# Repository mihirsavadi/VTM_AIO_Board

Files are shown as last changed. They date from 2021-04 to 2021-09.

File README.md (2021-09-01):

# All-in-One Board | Virginia Tech Motorsports



This repository contains all documentation and material related to [Virginia Tech's Formula SAE team - Virginia Tech Motorsports](https://vtmotorsports.weebly.com/) - All-in-One board for our 2021/2022 internal combustion vehicle.

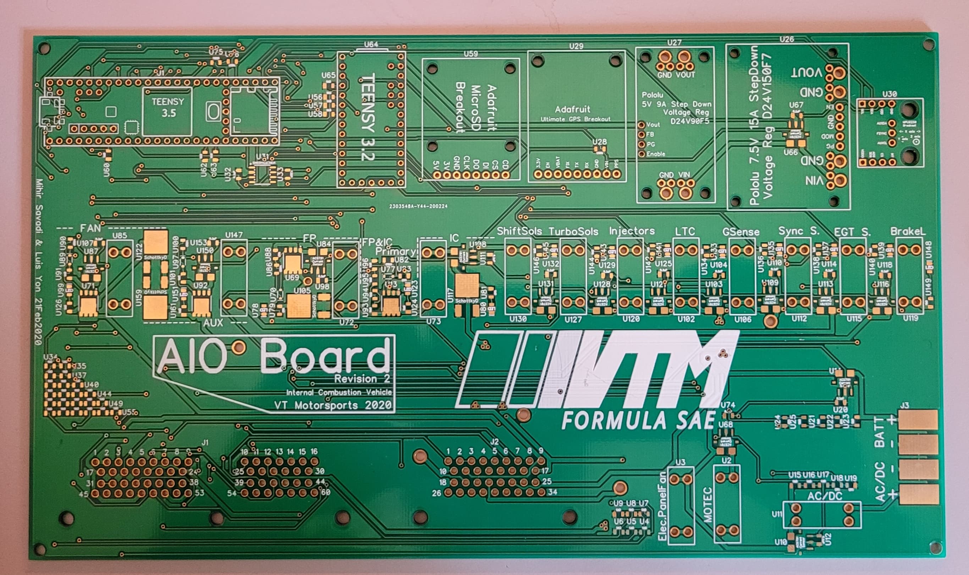
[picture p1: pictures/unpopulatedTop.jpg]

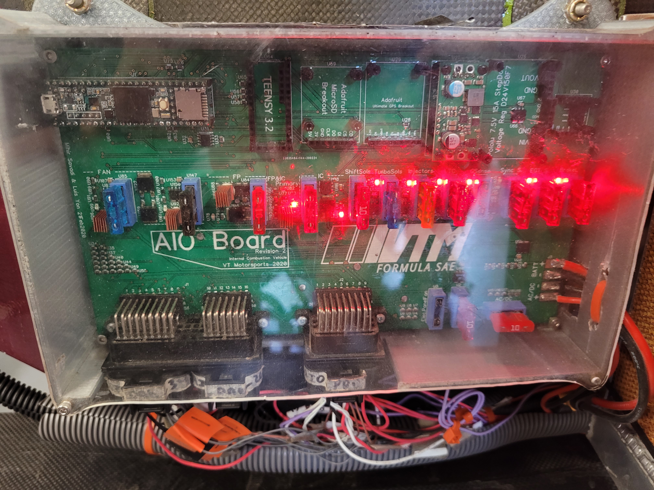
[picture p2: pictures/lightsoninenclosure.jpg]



The AIO board encapsulates several data acquisition features, as well as rules compliant power staging and power distribution, into a single PCB. Note that it is tightly integrated with our Brake-System-Plausibility device which can be found at the repository over [here](https://vtmotorsports.weebly.com/). 

The repository is split into [hardware](./hardware) and [software](./software) subdirectories. The former contains schematics, BOM, etc. Note that I used Diptrace as my PCB design software of choice, and while all critical files for board fabrication/inventory management are available in standard formats (GERBER, pdf's, spreadsheets), the original Diptrace files are included as well. The rest of the team uses Altium, however I prefer Diptrace - its easy to port between the two. The software directory contains Platform-IO project files that run both the MAIN and DRS microcontrollers on the AIO board. Custom Hardware Abstraction Layers/API's were made in order to make it easy to work with the board's slew of features. Both subdirectories include folders containing all our old revisions, which can be safely ignored unless you are a VTM member and/or are curious about the evolution of our design process.  

Running our microcontrollers with the Arduino bootloader and its general hardware abstraction layer not only allows us access to a vast array of arduino compatible easy-to-use libraries for various embedded hardware components (saving us dev time), but also allows lesser experienced team members to absorb functionality and hit the ground running with contribution quicker. We suffer from little to nothing when it comes to the typical drawbacks of using the arduino abstraction layer because 1. we are using proven and optimized hardware by standardizing to the teensy line of microcontrollers, 2. we are not using the stock arduino IDE, rather platform IO which is an extremely rich and ever-expanding IDE for a vast array of embedded processors and development boards, allowing us to easily and reliably integrate custom as well as off-the-shelf open source libraries, and 3. all of our applications are low speed and low memory.  

## Software Guide

Please read all the code in the /src directories for both the AIO_MAIN_MCU and AIO_DRS_MCU to understand the system thoroughly and before attempting to modify any code. All pin/IO definitions for the microcontrollers are established as macros in a file called "pin_definitions.hpp" in both directories, please study these and compare them with the schematics in the hardware subdirectories. Only use these macros for pin control in the code in order to keep things consistent, clean, and less error prone. Also remember to see header comments in order to match code and hardware compatibility - everything in the top level directories by default should be compatible with the latest hardware revision, which as of writing this is 'DAQ_PDU AIO BOARD REV2'.

In order to get an idea of how to use the various libraries to interact with peripherals on the AIO (SD card, GPS, IMU), read the documentation and example arduino sketches in the lib_dep directory. So for the MAIN MCU this would be [.pio\libdeps\teensy35](./software/AIO_MAIN_MCU/.pio/libdeps/teensy35)

If you want to add libraries, please visit the Platform-IO libraries registry and add the dependency into our project's 'platformio.ini' file. [This video](https://www.youtube.com/watch?v=buFKeqbafDI) illustrates this nicely. This file basically configures every option about our project - the serial port baud rate, library dependencies, what board etc were using, everything. Its a very powerful tool.  

Note that the arduino hardware abstraction layer compiles C++, but in reality most things are in C. The only significant usable C++ features are classes. Absolutely nothing from the C++ standard library should be used as it will wreck your boards memory and probably cause stack fragmentation which will either brick or freeze your board, which will be hard to debug. You can get away with using an std::string or an std::vector here or there but since its such a nasty slippery slope that hits quick stay away from it at all costs. So if you want to use convenient C++ like data structures (besides classes or structs) I recommend you don't. If you feel like you really must then its a sign your code is probably a tad too complicated for a simple embedded application such as ours - it might even mean you may be compromising on execution speed, which is bad given the primary purpose of software in this system being for data logging. [This](https://apprize.best/programming/arduino/10.html) is a nice resource regarding arduino programming and data structures.

I've tried my best to comment as much as possible, but if you have any questions reach out to me at mihirsavadi1@vt.edu.

## TODOS and Notes

- Add more pictures of the board to this readme, assembled as well as in enclosure (include wire jumps on the back)
- Implement BB method in DRS MCU class
- Implement IMU and GPS integration into the [aioMainMCU class](software/AIO_MAIN_MCU/src/aioMainMCU.cpp) (*integrated, not yet tested in hardware)
- Use RTC in GPS to get time data and add as a data point to CSV logging - IMPORTANT!
- Implement UART comms between DRS and MAIN MCU's
- Sort out CANBUS in MAIN MCU
- Clean up old revision subdirectories with information regarding what went wrong with them
- Include links to lecture videos describing entire system that we made (to youtube or something)
- Include wire map information here when that is all finalized and hashed out. 
- Add the CAD models for the AIO enclosure + BOM. Add a little window for a tiny fan for cooling, embedded flush into the enclosure.
- Add link to AIO breakdown documentation video

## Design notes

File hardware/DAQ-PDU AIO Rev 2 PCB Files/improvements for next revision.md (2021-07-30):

# IMPROVEMENTS FOR NEXT REVISION

- Order schematic net ports directions properly.  
- Steering position net goes into a non ADC port in the Main Teensy3.5, this is a dumb mistake.
- Change name of AIO instead of DAQ_PDU AIO.
- Use optoisolaters/optocouplers to buffer digital from power stages to mcu inputs, e.g. killsense on page 3 of schematic
- Fuse for servo connection
- Resistors u75 and u76 are 4.7k ohm but its attached to a pattern for a 360 resistor
- fill up middle gap make board dimensionally smaller
- maybe use raspberri pi pico or some rp2040 board and just one of them to replace both main mcu and teensy for parallel servo functionality (using the rp2040's PIO logic blocks)
- Use exclusively ACS781KLRTR-050B-T instead of the 150U's for greater resolution.
- Get rid of Batt and ACDC solder pads. Move literally all IO and power connections into superseal connections. Each superseal pin is good for 15A with normal thermal performance so unless really needed can just have one pin per V+ and GND. If need more just use another pin in parallel.
- Use up dead space in the middle a bit more.  
- Include a dedicated RTC instead of relying on GPS connection. Solder on directly since its a simple circuit. Can put under the GPS itself.
- CANBUS differential pair signals need to be routed more properly with impedance matching and such, even if lowspeed. See this video for guidance: https://www.youtube.com/watch?v=VRJI0X-6yTg

# Various Older Comments Dont Delete
Fuse only, from the highside (no two wires - grounded to a pin in motec) [current sensors in all]
	*!- 2x injectors
	*!- 2x turbo solenoids
	*!- 4x shifting solenoids
	!- brake light
	!- egt sensor
	!- sync sensor

Fuse only, but power AND ground [current sensors in all]
	*!- g sensor
	*!- lambda to can (LTC) unit
	*!- ignition coil 
	*!- motec (two power and two ground to split the current)

full blown power stages with mosfet (p channel for no reason other than its nicer i.e the specific one i found)
	*!- fan (with 2 sets of connectors left and right)
	*!- fuel pump
	*!- auxiliary 

^^^^^^^^^^^^^^^^^^^^^^^^^^^^^^^^^12V battery!^^^^^^^^^^^^^^^^^^^^^^^

**alternator also has current sensor.
**batter has beefy current sensor. 
^^^need to revise connection footprint.

------------------connectors need to add----------------
- engine kill switch repeat
- solenoid ground and kickback protection. (one wire from relay comes into button which grounds it). 

POWER NETS
+12V-
54-
55-
137-
66-
GND-
65-
64-
78-
138-
60-
164-
139-
46-
72-
119-
91-
71-
97-
68-
118-
122-
123-
130-
129-
127-
79-
124-
126-
+7.5V-
22-
50-
3-
4-
84-
135-
76-

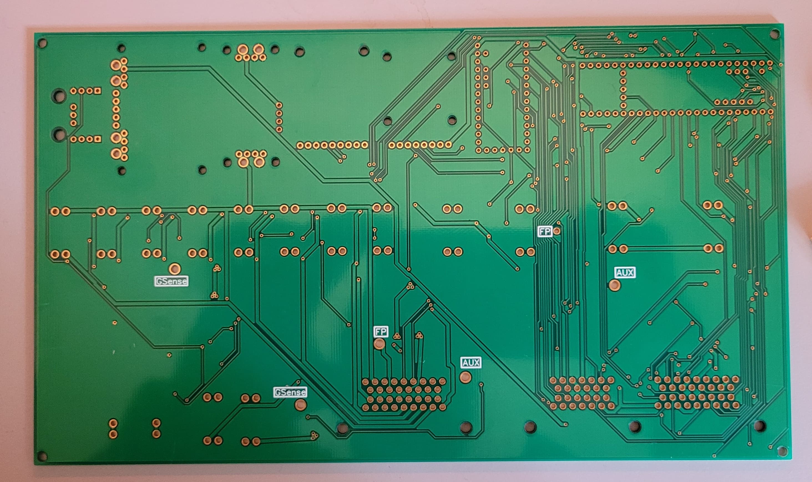
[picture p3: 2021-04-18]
pictures/unpopulatedBottom.jpg

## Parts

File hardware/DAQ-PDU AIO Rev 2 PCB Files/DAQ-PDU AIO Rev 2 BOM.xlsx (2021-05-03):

# | Name | RefDes | Quantity | Mfr No. | Datasheet
1 | Connector J1 60 Pin | J1 | 1 | 6437288-5 | https://www.mouser.com/ProductDetail/TE-Connectivity/6437288-5
2 | Connector J2 34 Pin | J2 | 1 | 3-6437285-1 | https://www.mouser.com/ProductDetail/TE-Connectivity/3-6437285-1
4 | Teensy 3.5 | U1 | 1
5 | Breaker Socket for E-T-A 1610-H2-15A | U2, U3, U11, U72, U73, U85, U102, U106, U112, U115, U119, U120, U127, U130, U147 | 15 | 3557-15 | https://www.mouser.com/ProductDetail/Keystone-Electronics/3557-15
6 | 1kO SMD0805 Resistor | U4, U5, U6, U7, U8, U9, U15, U16, U17, U18, U19, U21, U22, U23, U24, U25, U34, U35, U36, U37, U38, U39, U40, U41, U42, U43, U44, U45, U46, U47, U48, U49, U50, U51, U52, U53, U54, U55, U56, U57, U58, U60, U62, U63, U65, U79, U81, U83, U88, U91, U93, U94, U95, U96, U101, U124, U126, U134, U136, U138, U140, U142, U144, U146, U149, U161 | 66 | 0805W8J0102T5E | https://lcsc.com/product-detail/Chip-Resistor-Surface-Mount_Uniroyal-Elec-0805W8F1001T5E_C17513.html
7 | ACS781 50A bidirectional Current Sensor | U10, U14, U66, U68, U84, U87, U103, U108, U109, U113, U116, U121, U128, U131, U150 | 15 | ACS781KLRTR-050B-T | https://www.digikey.com/en/products/detail/allegro-microsystems/ACS781LLRTR-050B-T/6189096
8 | 0.1uF Cap SMD Ceramic | U12, U20, U32, U67, U74, U98, U104, U107, U110, U111, U114, U118, U125, U129, U132, U153 | 16 | TCC0805X7R104K500DT | https://lcsc.com/product-detail/Multilayer-Ceramic-Capacitors-MLCC-SMD-SMT_CCTC-TCC0805X7R104K500DT_C282732.html
9 | PChannel 40V100A | U13, U69, U71, U92 | 4 | SI7155DP-T1-GE3 | https://www.mouser.com/ProductDetail/Vishay-Siliconix/SI7155DP-T1-GE3
10 | 7.5V 15A StepdownRegulator D24V150F7 | U26 | 1 |  | https://www.pololu.com/product/2883
11 | 5V 9A Stepdown Regulator D24V90F5 | U27 | 1 | D24V90F5 | https://www.pololu.com/product/2866
12 | 4.7kO SMD0805 Resistor | U28, U75, U76 | 3 | RC0805FR-074K7L | https://www.mouser.com/ProductDetail/Yageo/RC0805FR-074K7L
13 | Ultimate GPS Breakout | U29 | 1 |  | https://www.adafruit.com/product/746
14 | MPU9250 IMU Breakout | U30 | 1 |  | https://www.sparkfun.com/products/13762
15 | SN65HVD230DR CANBUS Transciever | U31 | 1 |  | https://lcsc.com/product-detail/CAN_TI_SN65HVD230DR_SN65HVD230DR_C12084.html
16 | 120O SMD0805 Resistor | U33 | 1 |  | https://lcsc.com/product-detail/Chip-Resistor-Surface-Mount_Uniroyal-Elec-0805W8F1200T5E_C17437.html
17 | MicroSD Card Reader | U59 | 1 |  | https://www.adafruit.com/product/254
18 | Teensy 3.2 | U64 | 1
19 | SchottkyD 40V1A | U70, U77, U89, U97 | 4 | B5819WS | https://lcsc.com/product-detail/Schottky-Barrier-Diodes-SBD_MDD-Microdiode-Electronics-B5819WS_C64886.html
20 | Red 20mA LED 0805 SMD | U78, U80, U99, U123, U133, U135, U137, U139, U141, U143, U145, U148, U151 | 13 | 17-21SURC/S530-A3/TR8 | https://lcsc.com/product-detail/Light-Emitting-Diodes-LED_0805-Red-LED-Iv-61mcd-Typ-atIF-20mA_C72037.html
21 | 100O SMD0805 Resistor | U82, U86, U90, U100 | 4 | RTT05101JTP | https://lcsc.com/product-detail/Chip-Resistor-Surface-Mount_100R-101-5_C103909.html
22 | Schottky Diode 60V100A | U105, U117, U122, U159 | 4 | RBR15BM60AFHTL | https://www.mouser.com/ProductDetail/ROHM-Semiconductor/RBR15BM60AFHTL
 | Brake Bias Toggle Switch (NKK Switches) |  |  | M2028TJW01-GA-1A | https://www.mouser.com/ProductDetail/NKK-Switches/M2028TJW01-GA-1A?qs=HrqAcaC9xK5l%252BLLRcEF4FQ%3D%3D

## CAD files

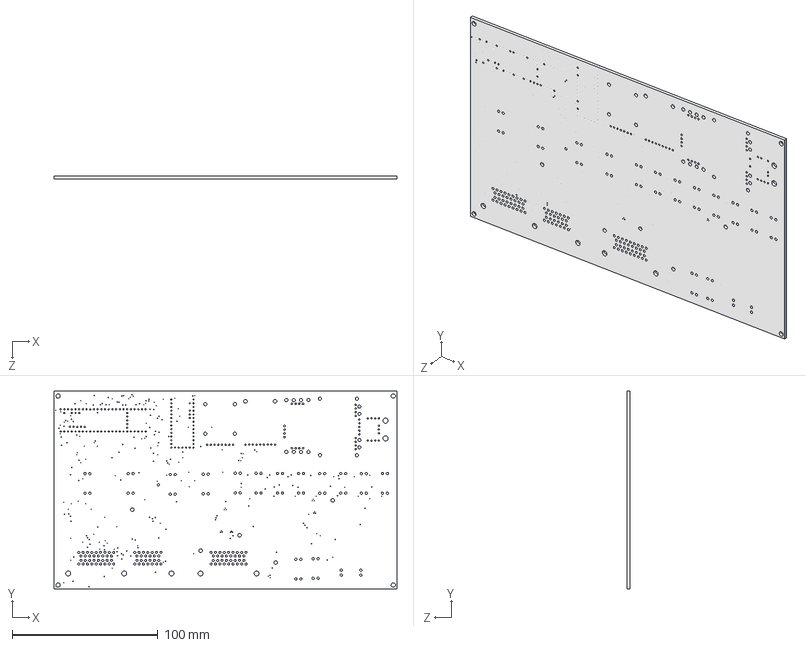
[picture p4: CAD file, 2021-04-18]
hardware/DAQ-PDU AIO Rev 2 PCB Files/DAQ-PDU AIO Rev2 3D Model.step
235.8 x 135.8 x 2.00 mm

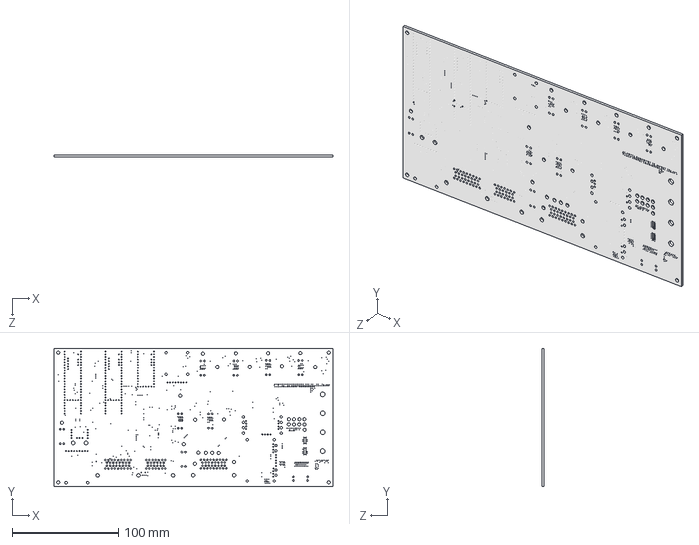
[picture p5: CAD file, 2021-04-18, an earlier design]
hardware/Old Revisions Documents/DAQ-PDU AIO Rev 1.1 PCB FILES/3D Models & Enclosures/DAQ-PDU AIO Rev1.1 3D Model.step
262.5 x 130.0 x 2.00 mm

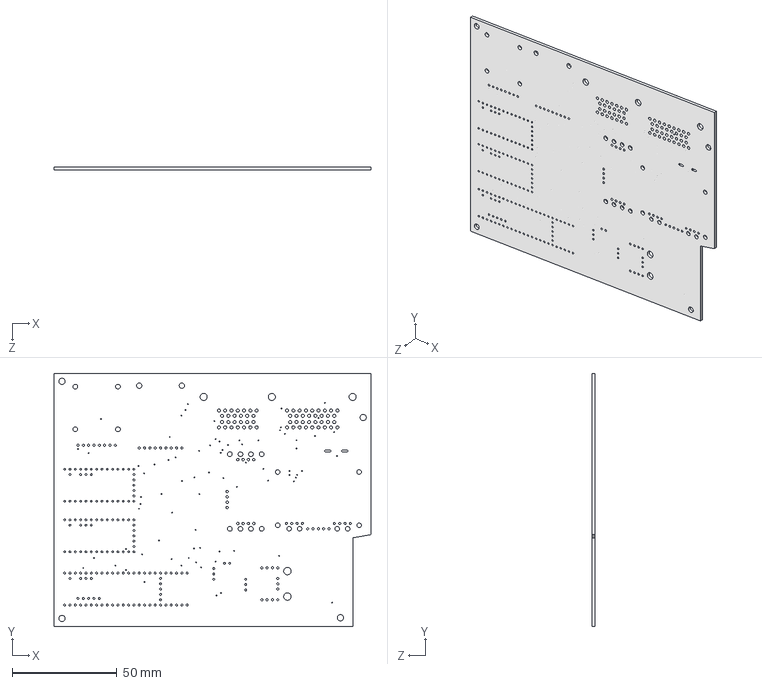
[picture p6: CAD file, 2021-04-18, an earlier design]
hardware/Old Revisions Documents/Old Data Aquisition Designs/DAQ Rev 2 Board/DAQ Rev 2 3D Model.step
151.1 x 120.7 x 1.59 mm

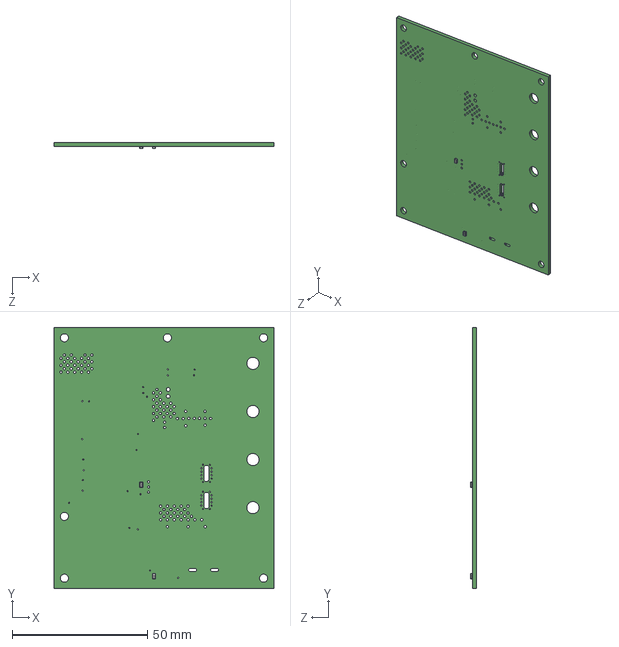
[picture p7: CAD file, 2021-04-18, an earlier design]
hardware/Old Revisions Documents/Old Power Distribution Unit Designs/PDU Rev 2/Starter Rev 2 PCB 3D Model.step
81.3 x 96.5 x 2.37 mm
Board_Starter_Rev_2_PCB_3D_Model
User_Library-0805_SMD_Resistor x 2

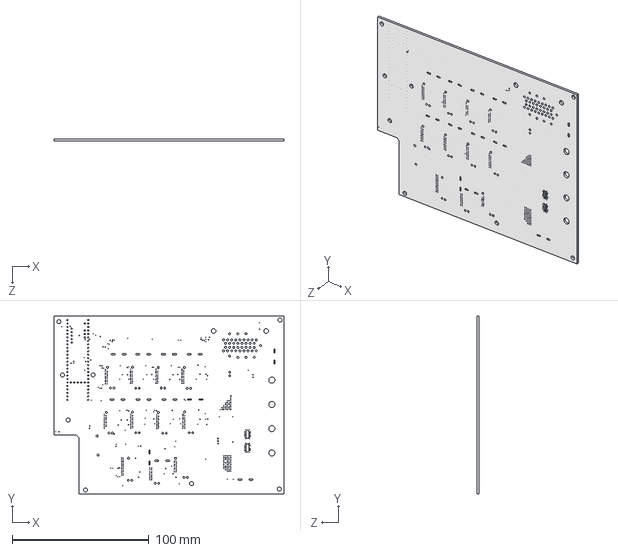
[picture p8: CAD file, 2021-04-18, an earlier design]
hardware/Old Revisions Documents/Old Power Distribution Unit Designs/PDU Rev 3/PDU Rev 3 3D Model.step
168.4 x 130.0 x 1.59 mm

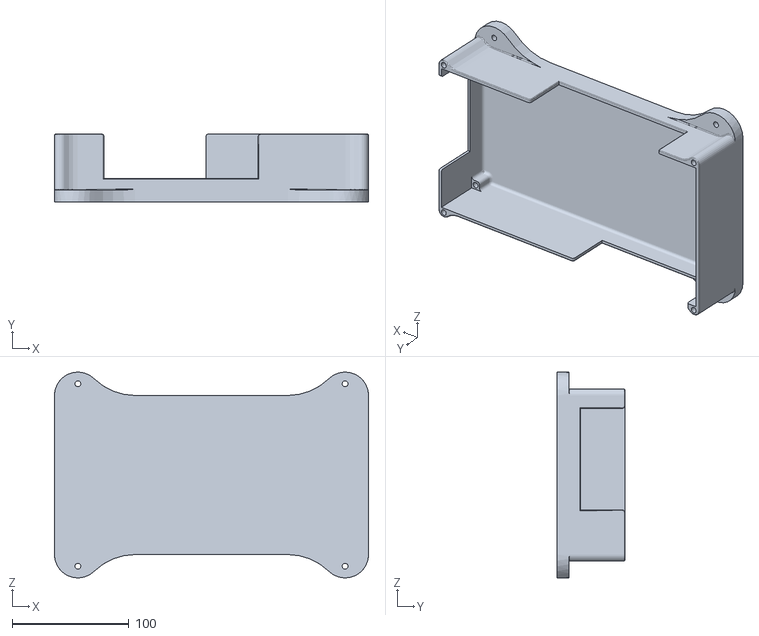
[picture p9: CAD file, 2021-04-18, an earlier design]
hardware/Old Revisions Documents/DAQ-PDU AIO Rev 1.1 PCB FILES/3D Models & Enclosures/DAQ-PDU AIO Rev1.1 Enclosure Base.stl
268.5 x 58.0 x 176.0

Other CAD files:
hardware/Old Revisions Documents/DAQ-PDU AIO Rev 1.1 PCB FILES/3D Models & Enclosures/DAQ-PDU AIO Rev1.1 Enclosure Base.dwg
hardware/Old Revisions Documents/DAQ-PDU AIO Rev 1.1 PCB FILES/3D Models & Enclosures/DAQ-PDU AIO Rev1.1 Enclosure Base.skp

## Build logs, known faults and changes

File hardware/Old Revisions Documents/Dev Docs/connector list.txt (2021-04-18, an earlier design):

A1. Universal Ground
A2. MOTEC 0V Engine
A3. 12V+ for MOTEC
A4. GND for MOTEC
A5. 5V+ for BSPD
A6. GND for BSPD
A7. BSPD Fault Indicator Input
A8. Kill Sense Signal Output to BSPD
A9. BSPD FP&IC Relay Switch +
A10. BSPD FP&IC Relay Switch --
A11. Throttle Pedal Pot 1 Signal (from BSPD)
A12. Brake Pressure Sensor Signal (from BSPD)
A13. 5V+ for Dash Display
A14. GND for Dash Display 
A15. TX to Dash Display 
A16. RX from Dash Display
A17. 5V+ for Telemetry
A18. GND for Telemetry
A19. TX to Telemetry
A20. RX from Telemetry
A21. 7.5V+ for DRS Servo
A22. GND for DRS Servo
A23. Signal to DRS Servo
A24. 7.5V+ for Brake Bias Servo
A25. GND for Brake Bias Servo
A26. Signal for Brake Bias Servo
A27. 12V+ for Electrical Panel Fan
A28. GND for Electrical Panel Fan
A29. Steering Position Pot 3.3V+
A30. Steering Position Pot GND
A31. Steering Position Pot Signal
A32. Steering Position Repeat to MOTEC from DAC0
A33. Gear Signal N
A34. Gear Signal 1
A35. Gear Signal 2
A36. Gear Signal 3
A37. Gear Signal 4
A38. Gear Signal 5
A39. Gear Sense output to MOTEC
A40. Nuetral Button Repeat to MOTEC
A41. Launch Control Button Repeat to MOTEC
A42. CANBUS GND
A43. CANBUS LOW
A44. CANBUS HIGH
A45. Brale Bias ToggleSwitch InPin 2
A46. Brake Bias ToggleSwitch OutPin 1
A47. Brake Bias ToggleSwitch OutPin 4
A48. Brake Bias ToggleSwitch OutPin 6
A49. DRS Button +
A50. DRS Button --
A51. Nuetral Button +
A52. Nuetral Button --
A53. Launch Control Button +
A54. Launch Control Button --
A55. Data Log Toggle Switch +
A56. Data Log Toggle Switch --
A57. Engine Kill Switch +
A58. Engine Kill Switch --
A59. Crank Switch +
A60. Crank Switch -

B1. BOTS Switch +
B2. BOTS Sitch --
B3. Cockpit Kill Switch +
B4. Cockpit Kill Switch --
B5. Fuel Pump Enable Signal from MOTEC
B6. Fan Enable Signal from MOTEC
B7. Auxiliary1 Enable Signal from MOTEC
B8. Auxiliary2 Enable Signal from MOTEC
B9. FAN GROUP 1 +
B10. FAN GROUP 1 --
B11. FAN GROUP 2 +
B12. FAN GROUP 2 --
B13. IGNITION COIL +
B14. IGNITION COIL --
B15. FUEL PUMP +
B16. FUEL PUMP --
B17. LAMBDA SENSOR +
B18. LAMBDA SENSOR --
B19. AUXILIARY1 +
B20. AUXILIARY1 --
B21. AUXILIARY2 +
B22. AUXILIARY2 --
B23. 
B24.
B25.
B26. 
B27.
B28.
B29. 
B30.
B31.
B32.
B33.
B34. 

C1. AC/DC +
C2. AC/DC --
C3. BATT +
C4. BATT --
C5. Starter Motor +
C6. Starter Motor --

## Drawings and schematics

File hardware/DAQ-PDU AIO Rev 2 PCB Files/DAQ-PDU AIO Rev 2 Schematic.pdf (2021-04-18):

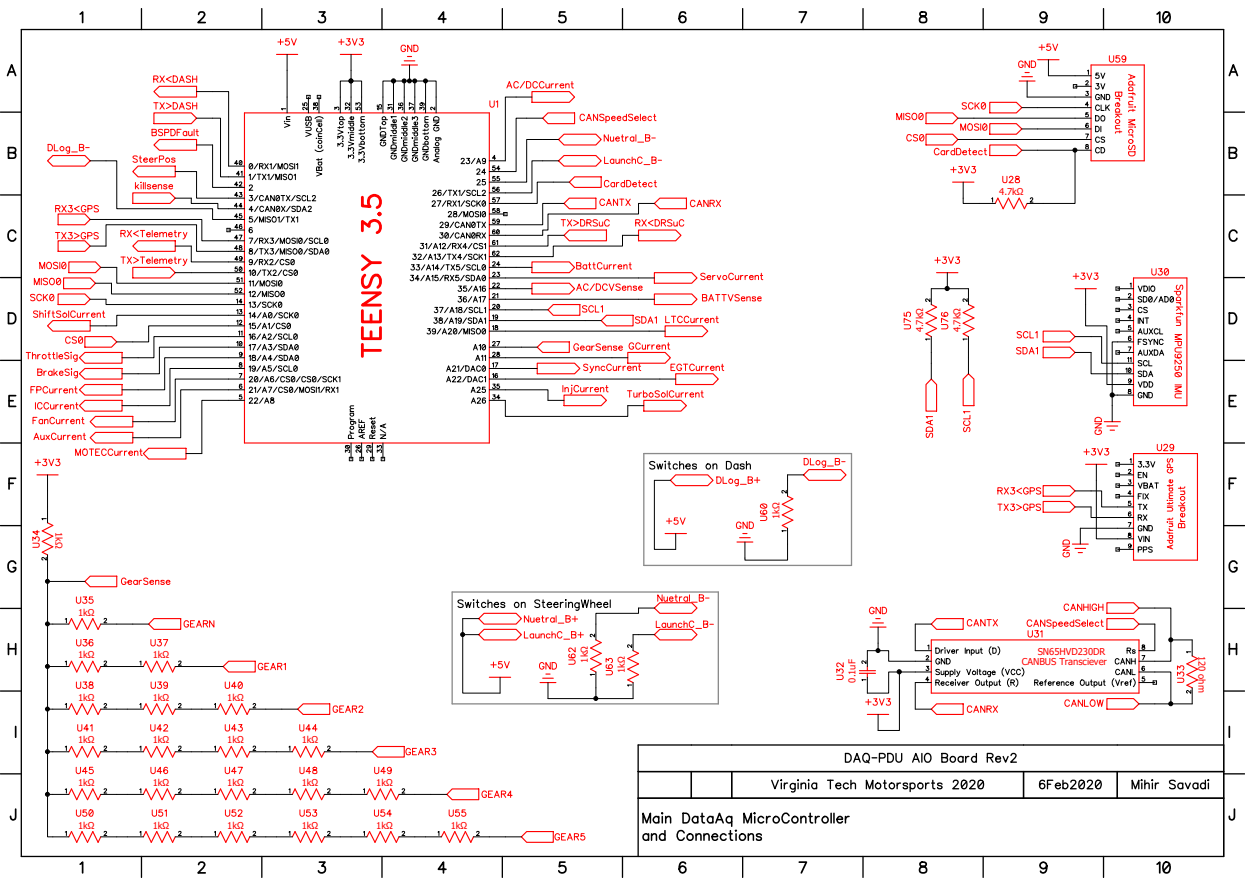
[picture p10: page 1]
SN65HVD230DR; CANBUS Transciever 0.1uF; 120 ohm ¹kΩ

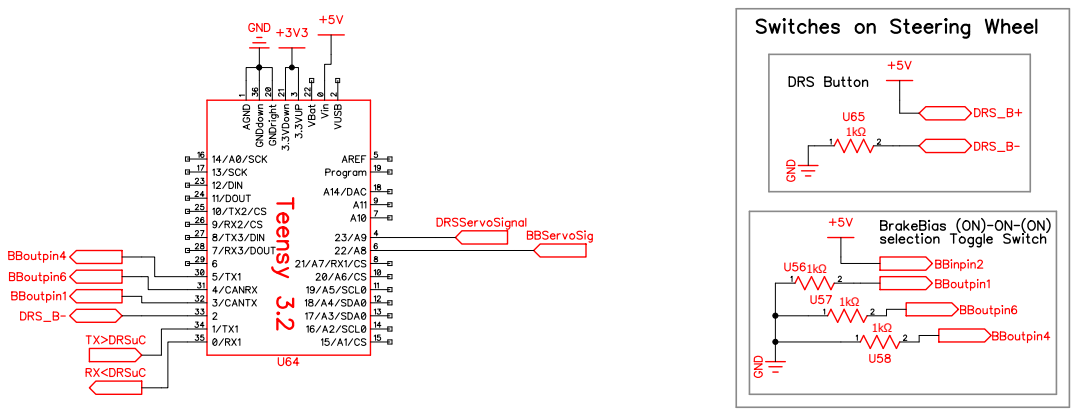
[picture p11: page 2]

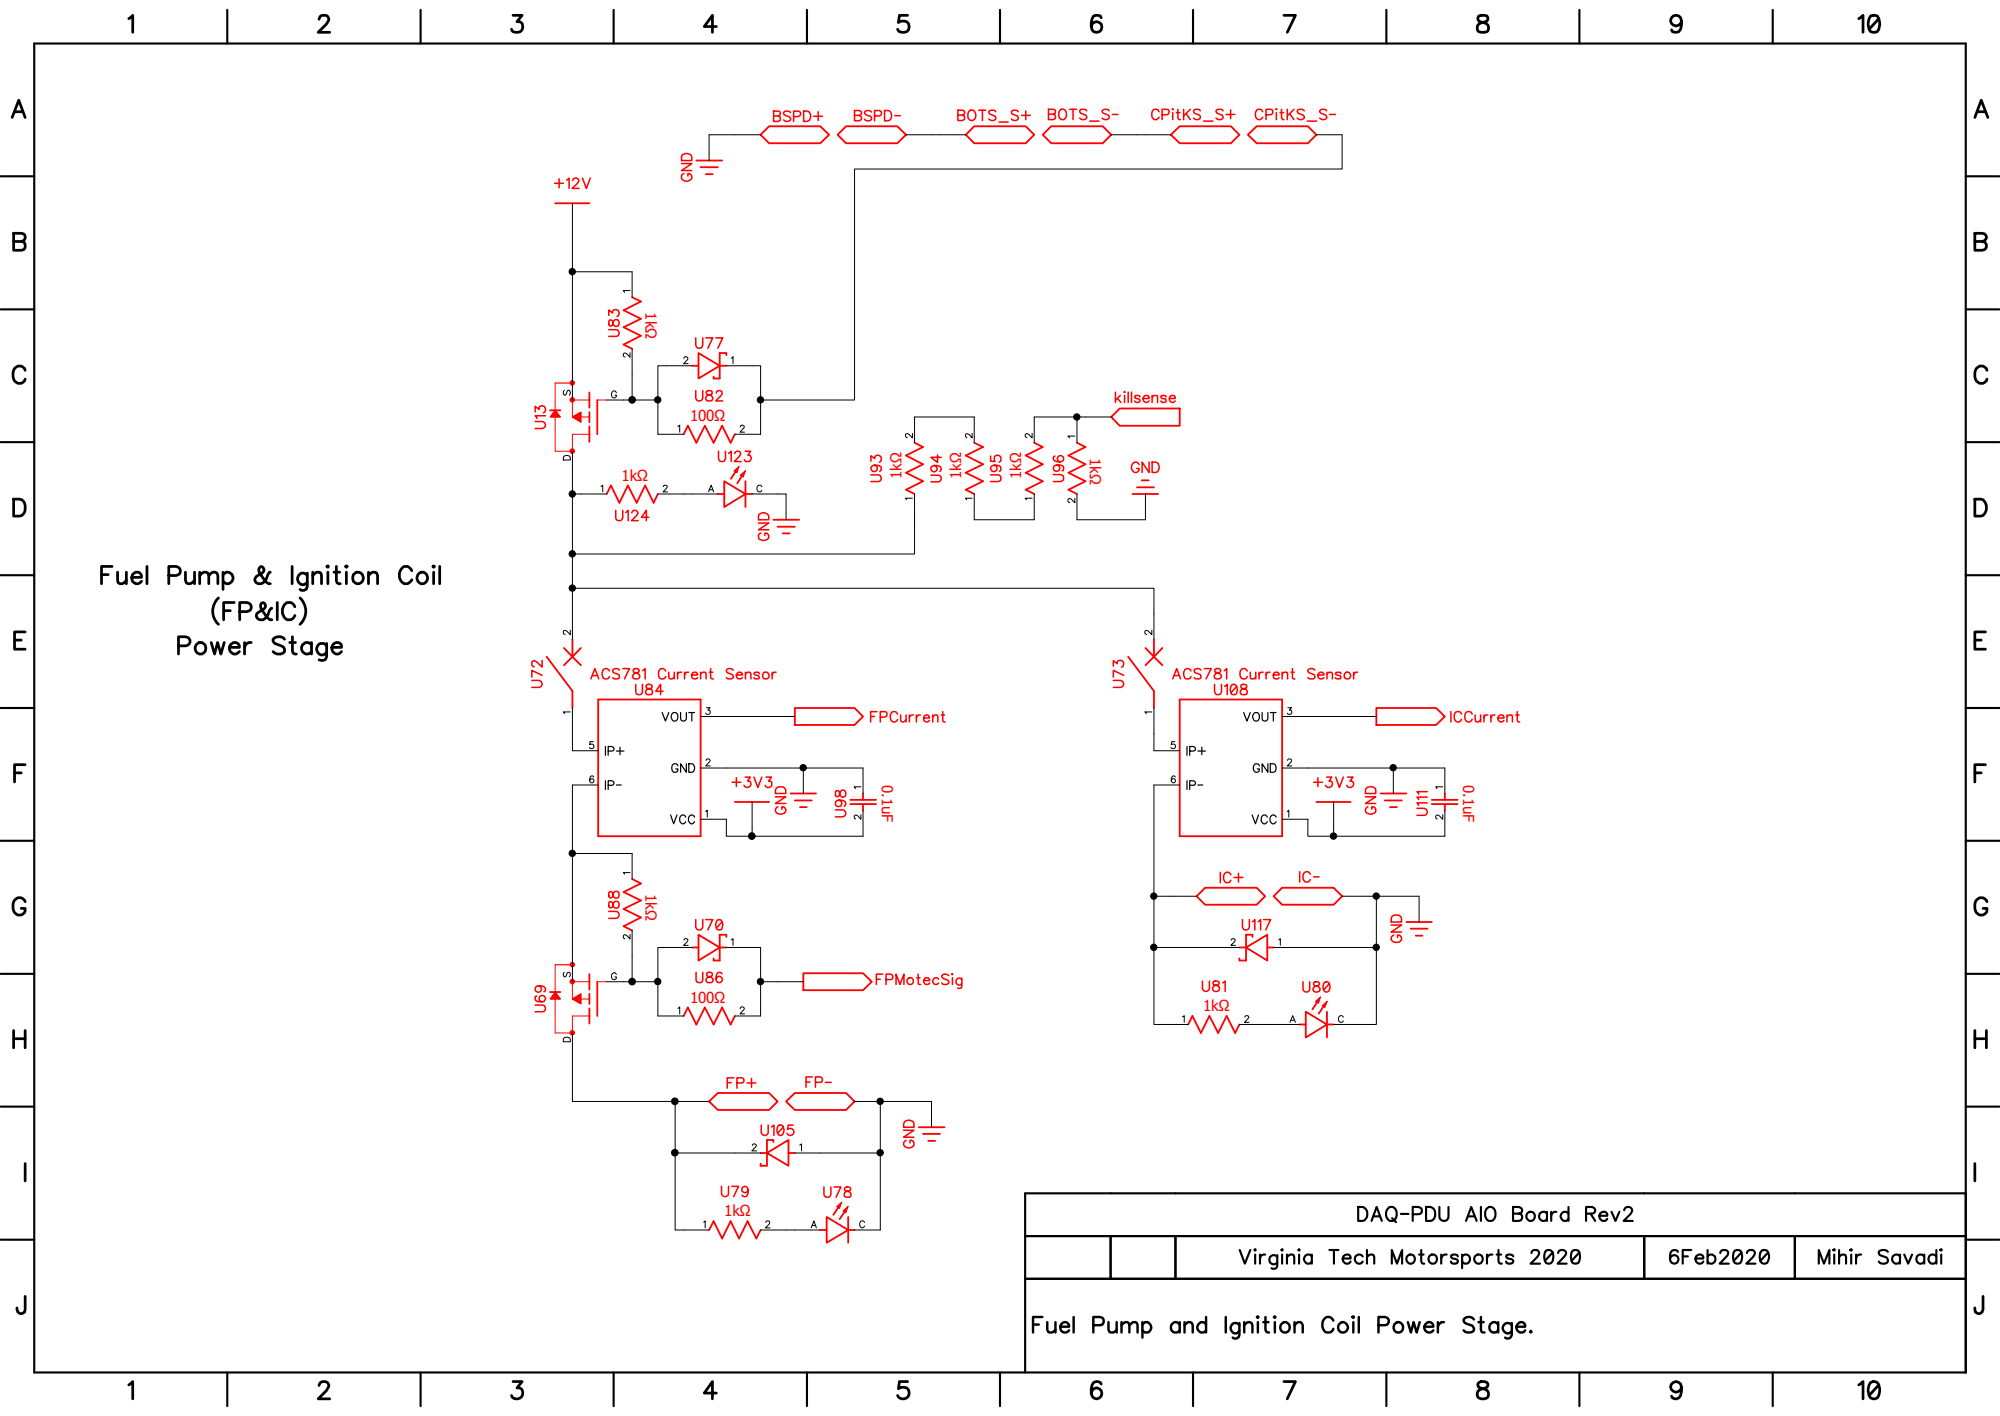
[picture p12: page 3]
100Ω ¹kΩ

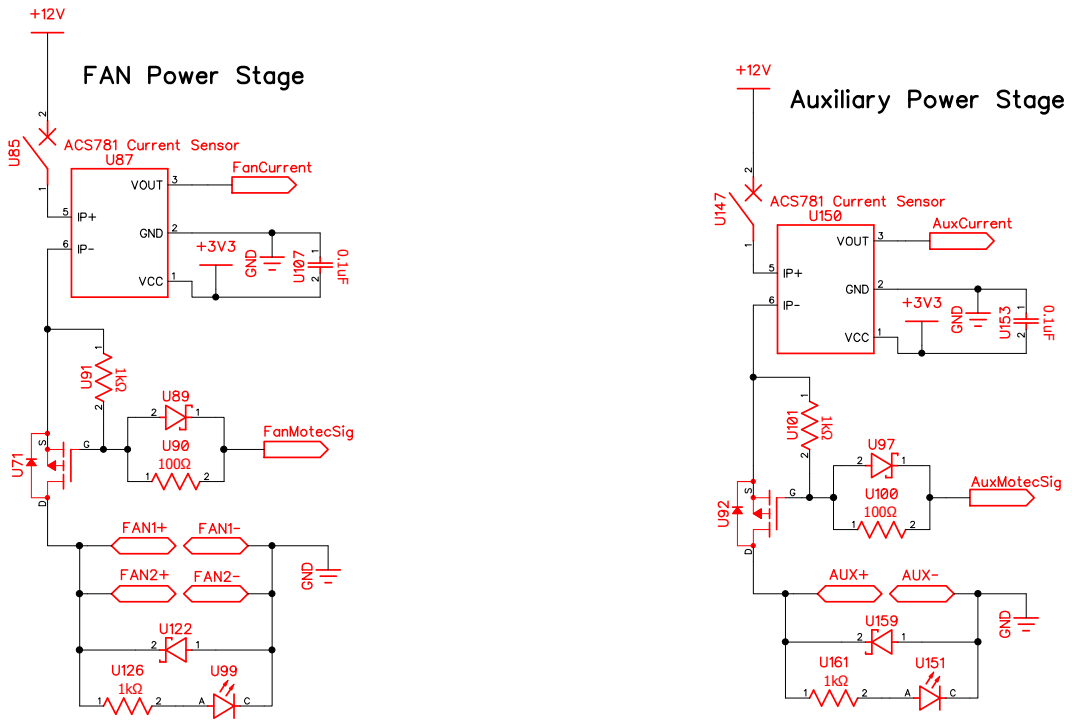
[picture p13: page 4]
100Ω ¹kΩ; 100Ω ¹kΩ ⁰.1uF

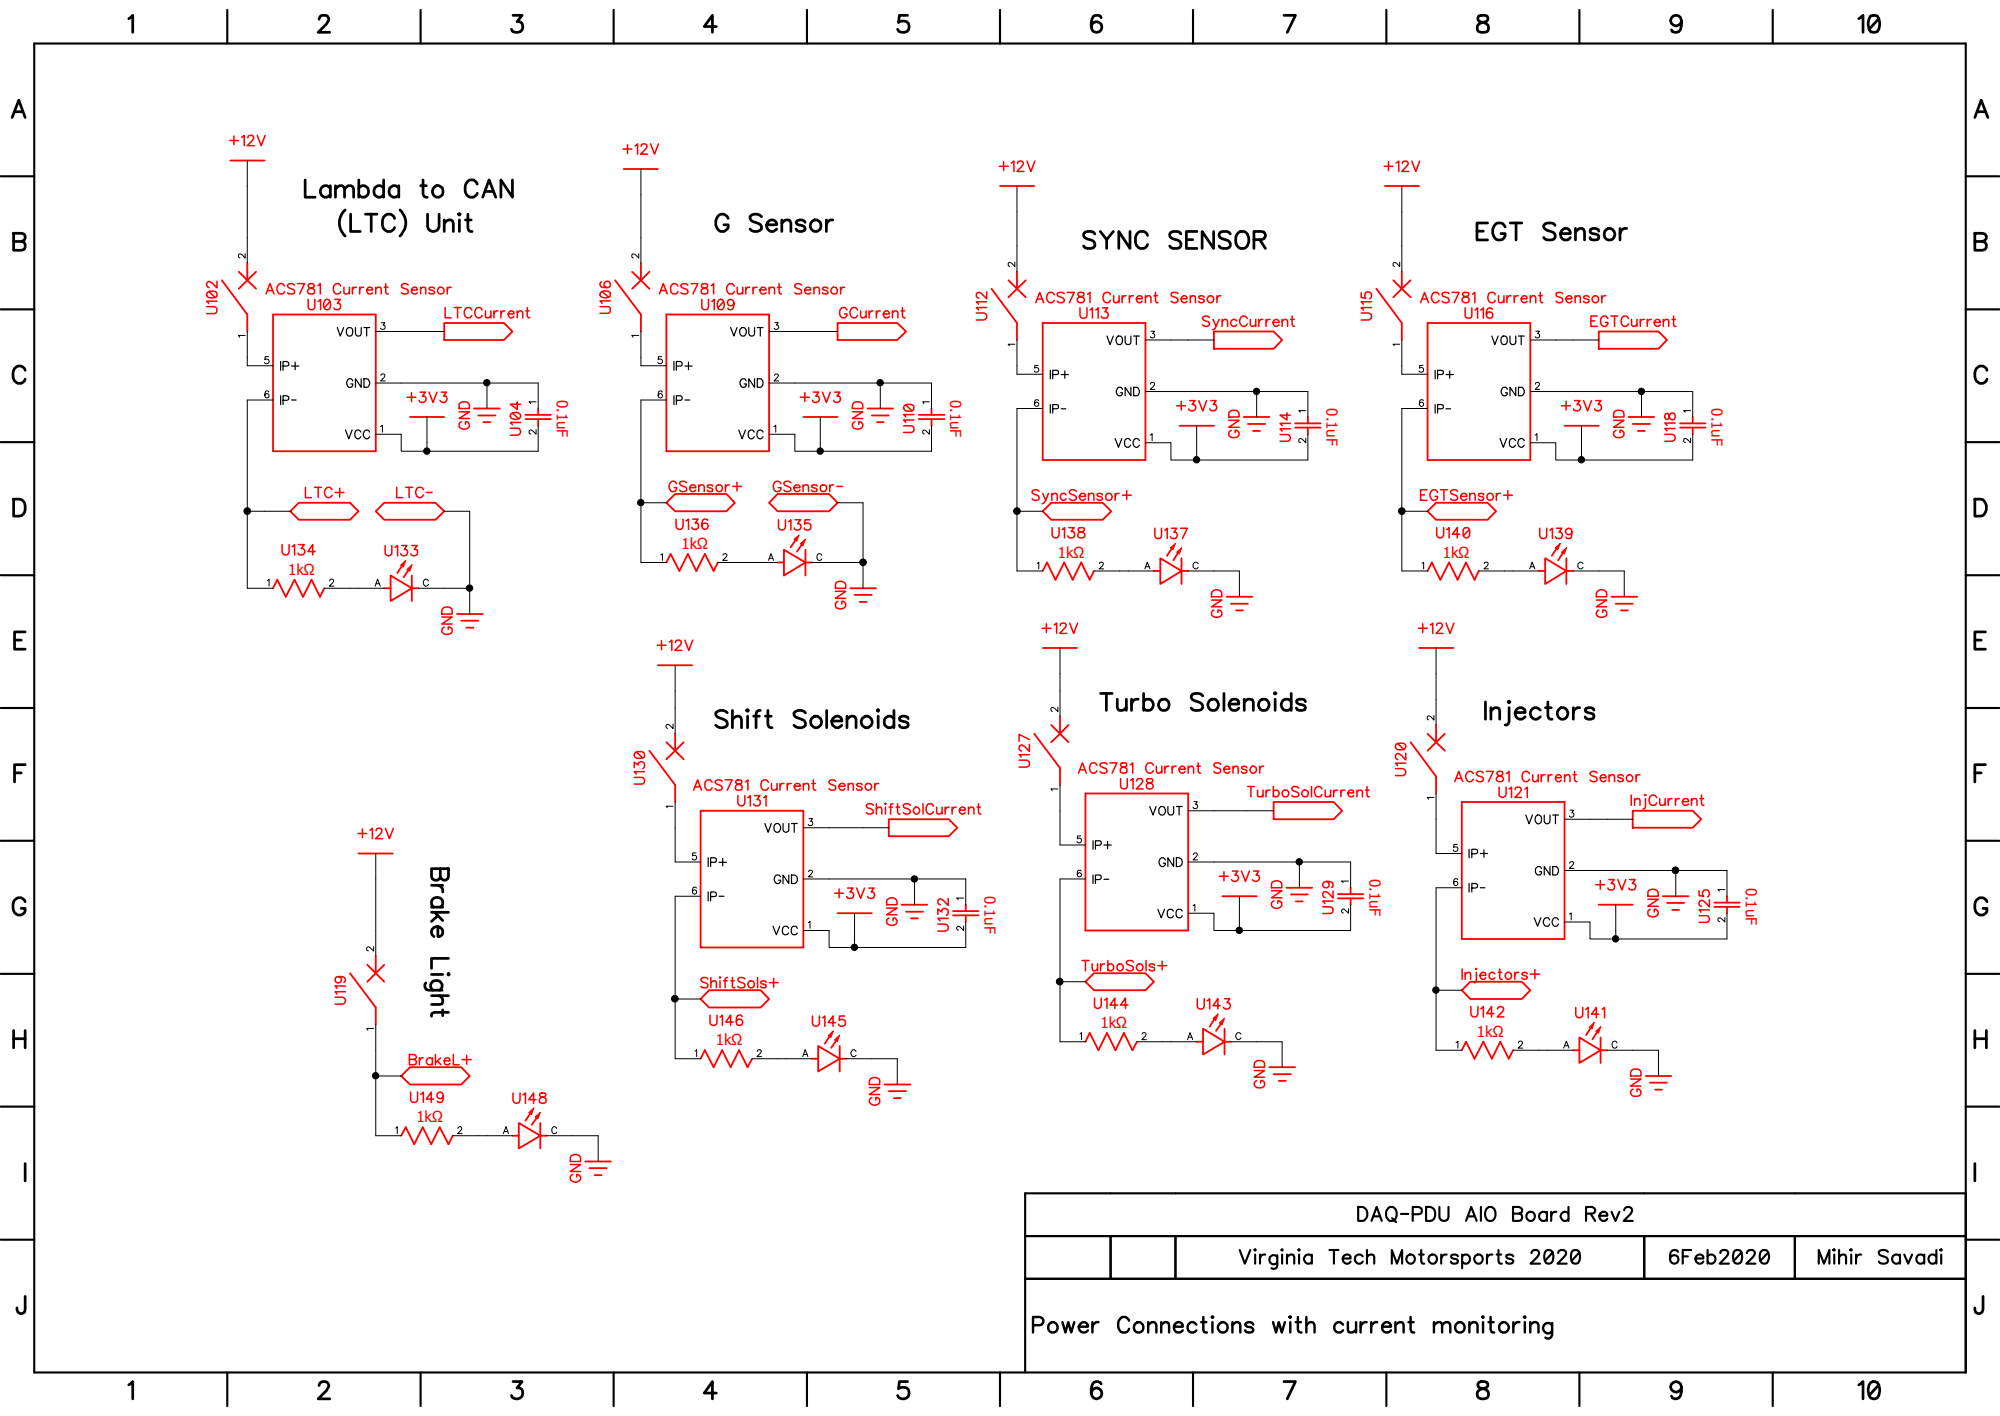
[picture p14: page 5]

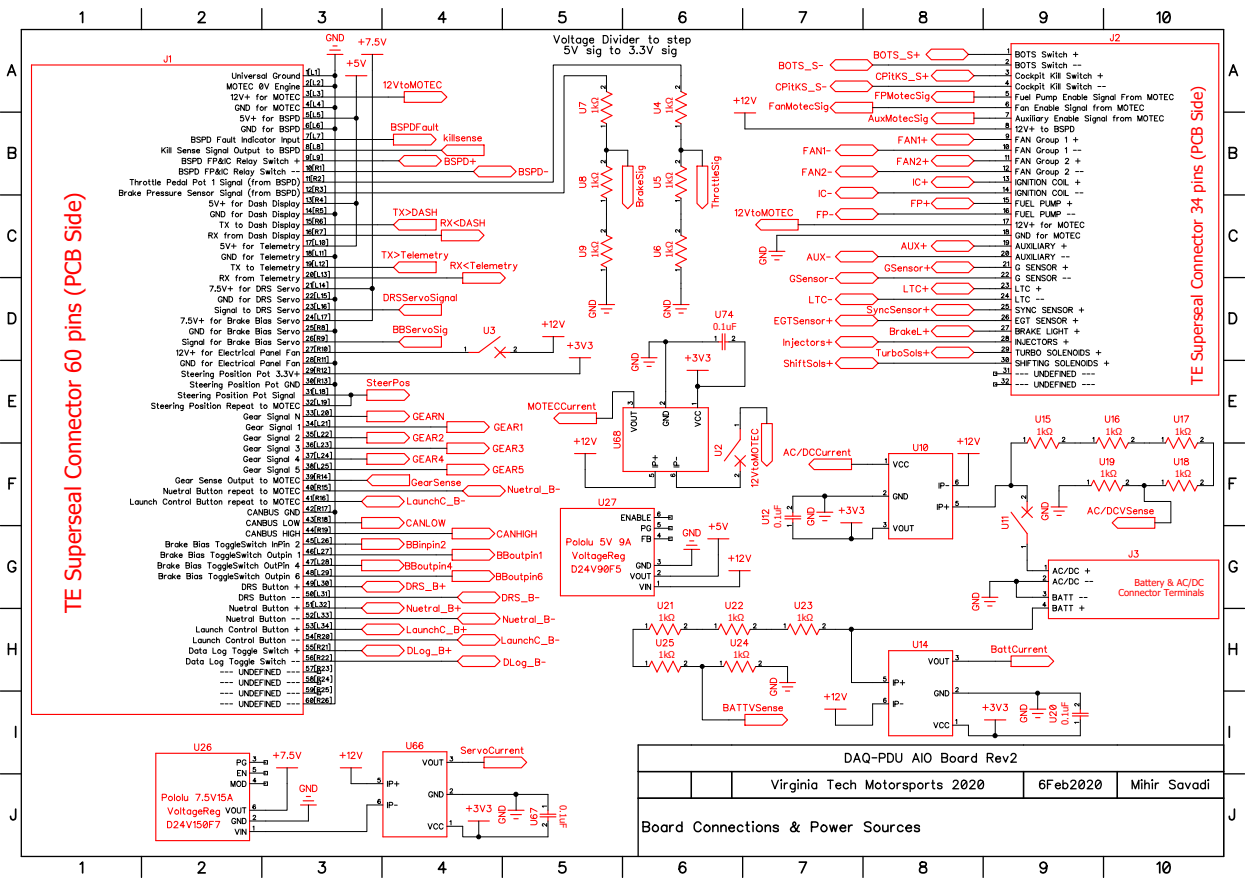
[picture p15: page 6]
Connector Terminals ¹kΩ 1kΩ 1kΩ ¹kΩ 1kΩ 1kΩ

TE Superseal Connector 60 pins (PCB Side) TE Superseal Connector 34 pins (PCB Side)

Battery & AC/DC

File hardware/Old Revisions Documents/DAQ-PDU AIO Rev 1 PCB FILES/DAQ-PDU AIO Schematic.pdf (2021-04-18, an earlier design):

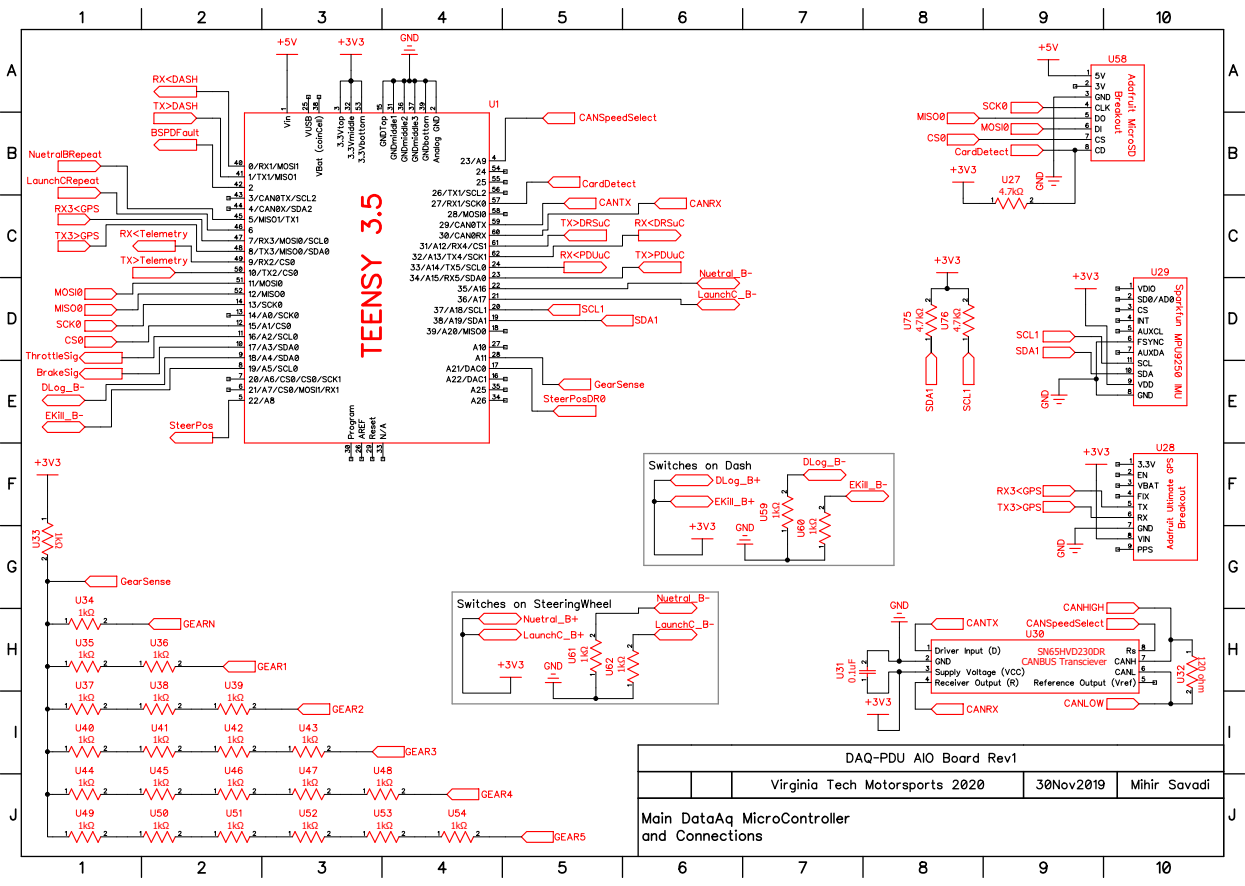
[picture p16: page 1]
SN65HVD230DR; CANBUS Transciever 0.1uF; 120 ohm ¹kΩ

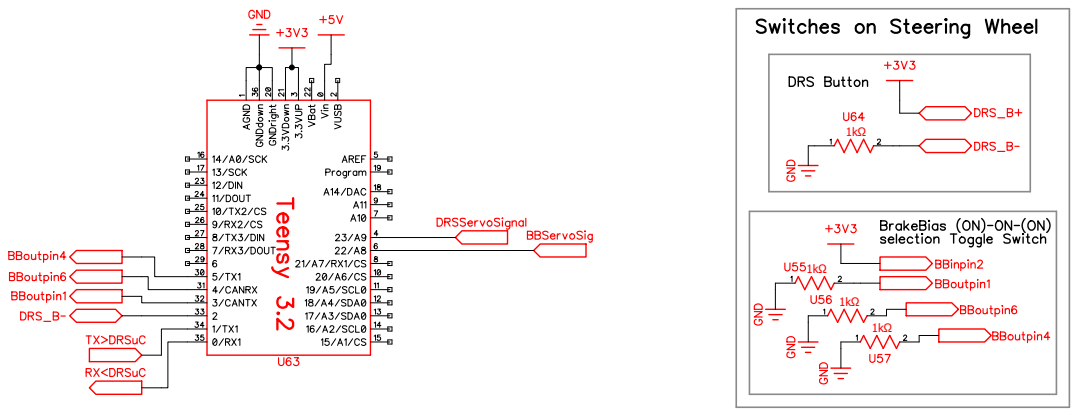
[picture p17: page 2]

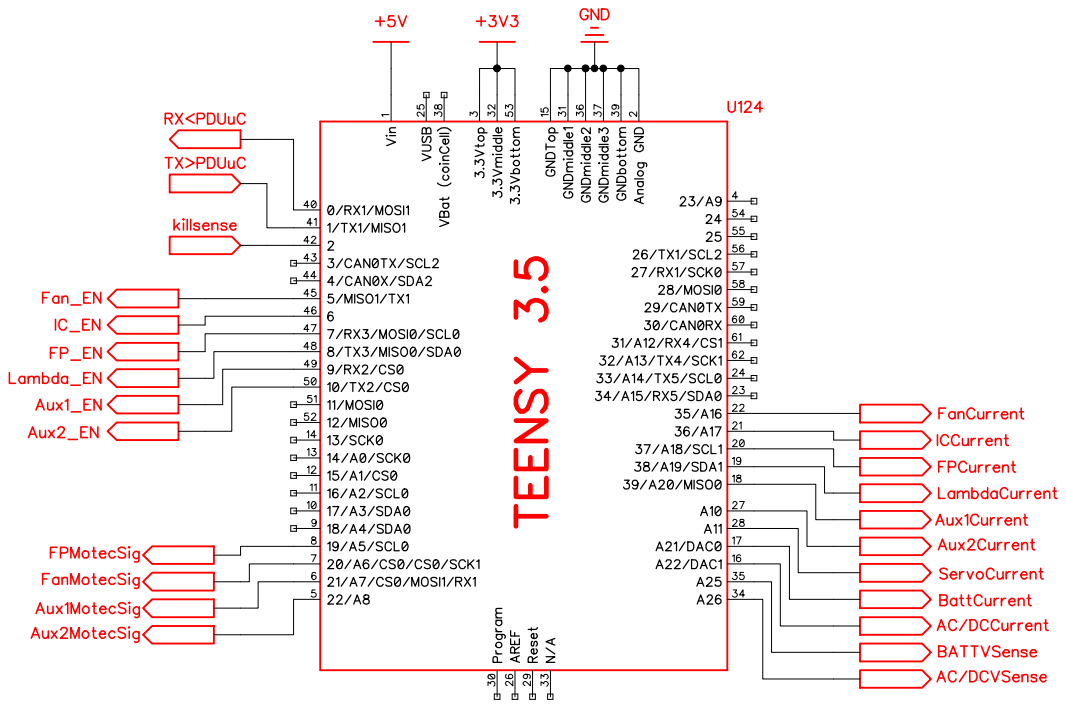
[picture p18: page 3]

# 4.7uF 100kΩ

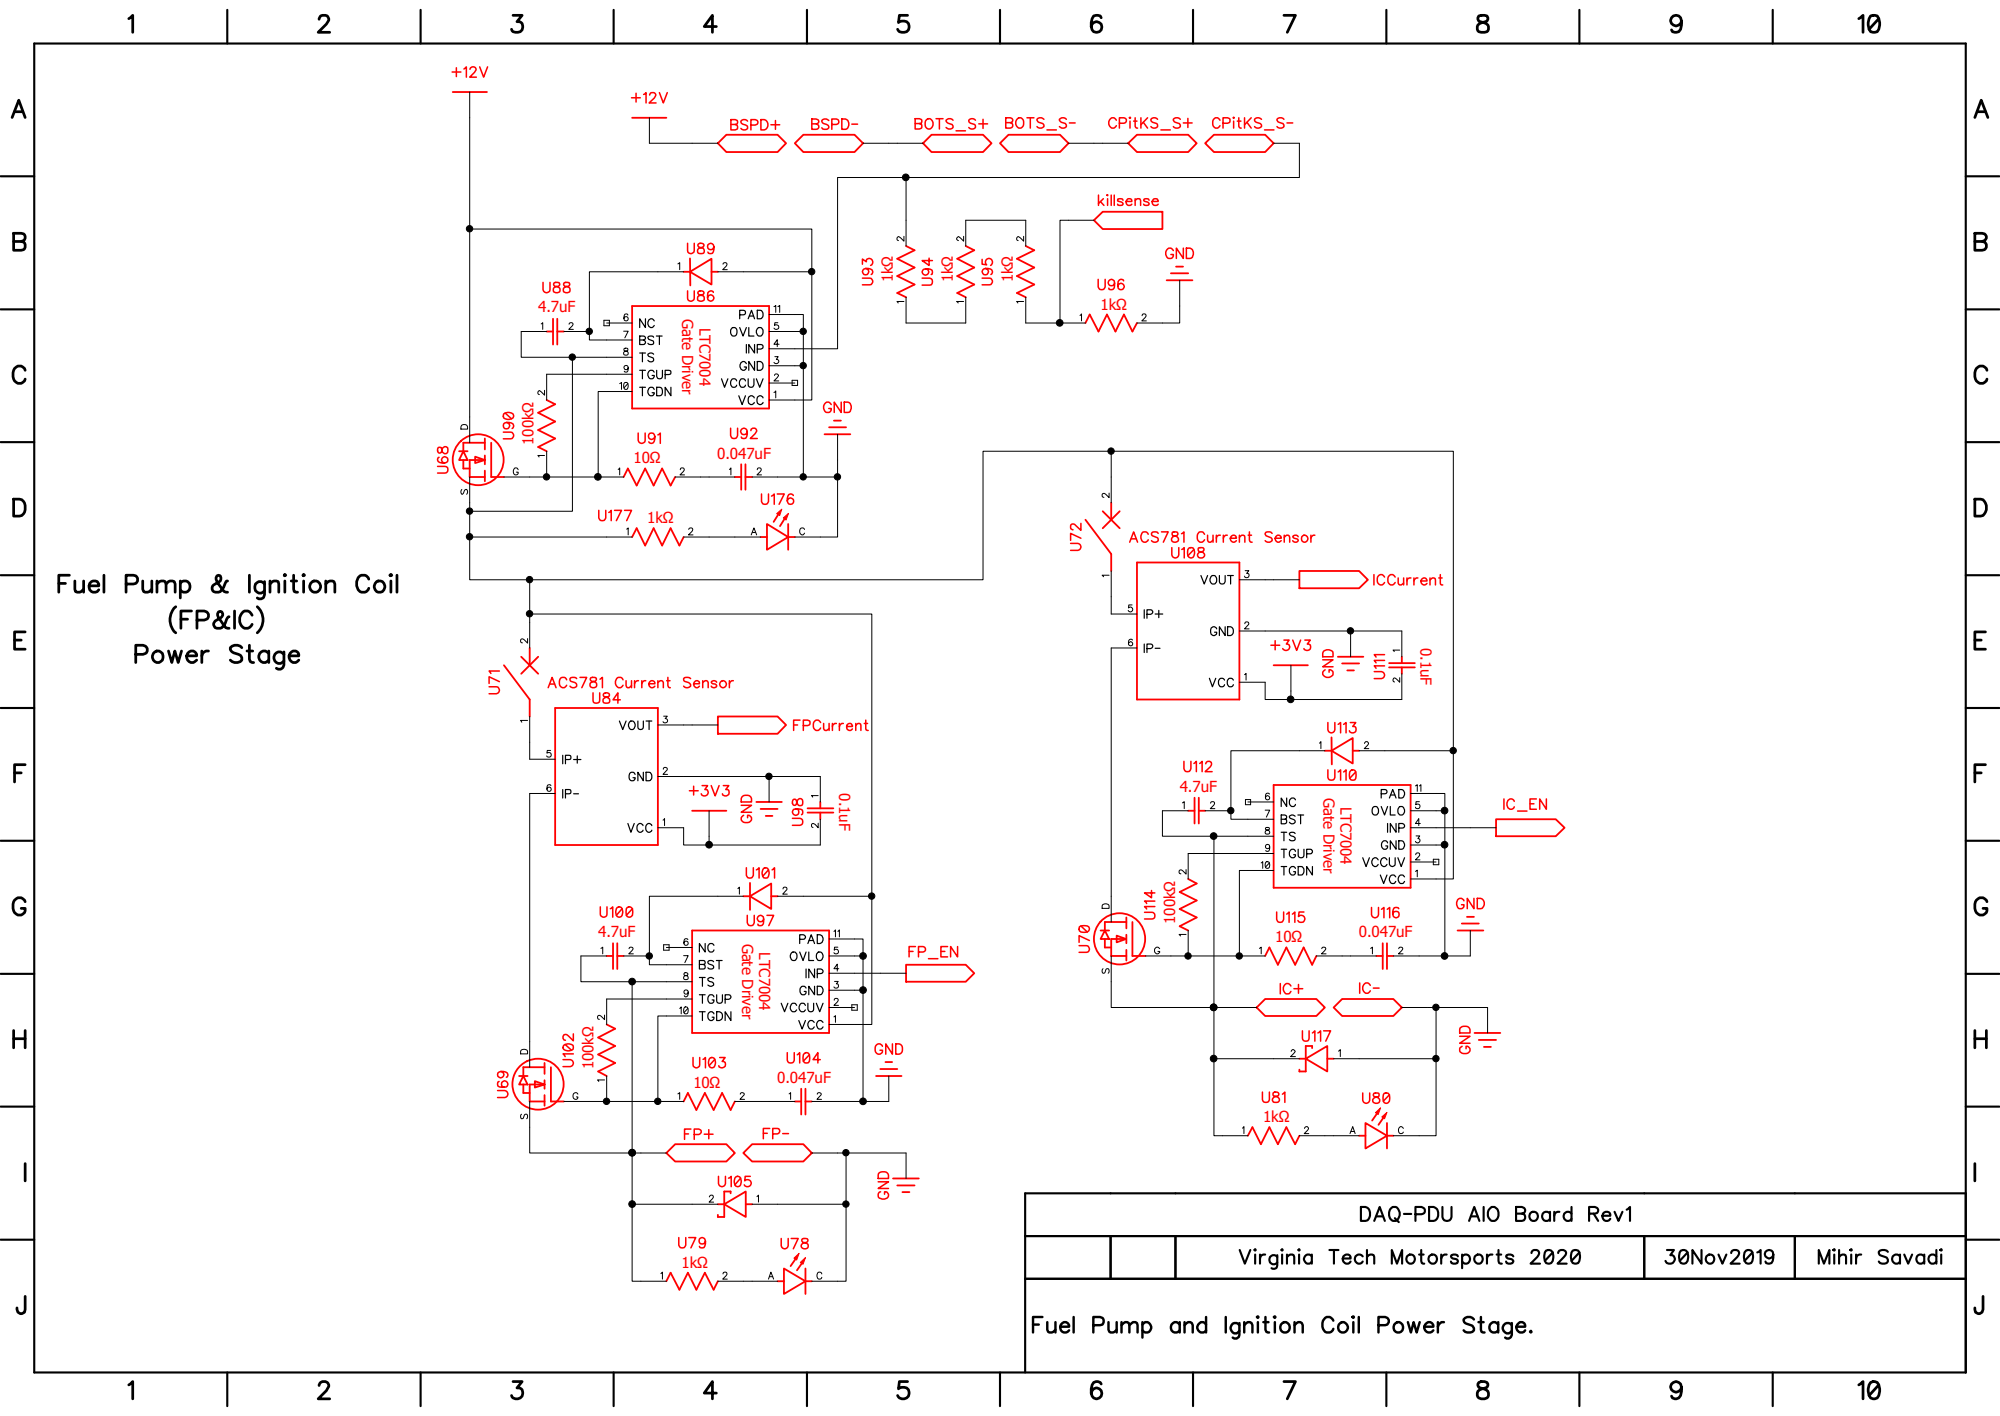
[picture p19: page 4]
1kΩ LTC7004 Gate Driver; LTC7004 Gate Driver

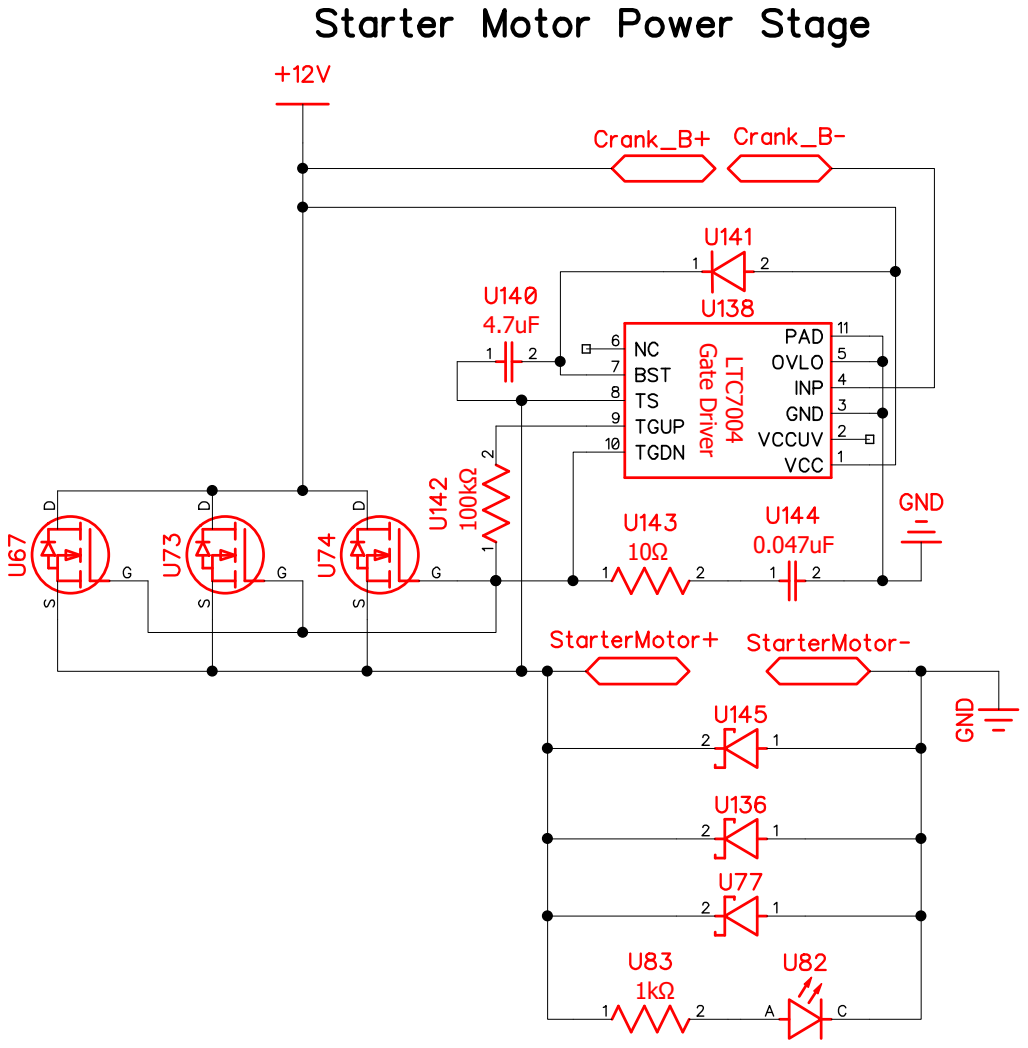
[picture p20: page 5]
LTC7004 Gate Driver

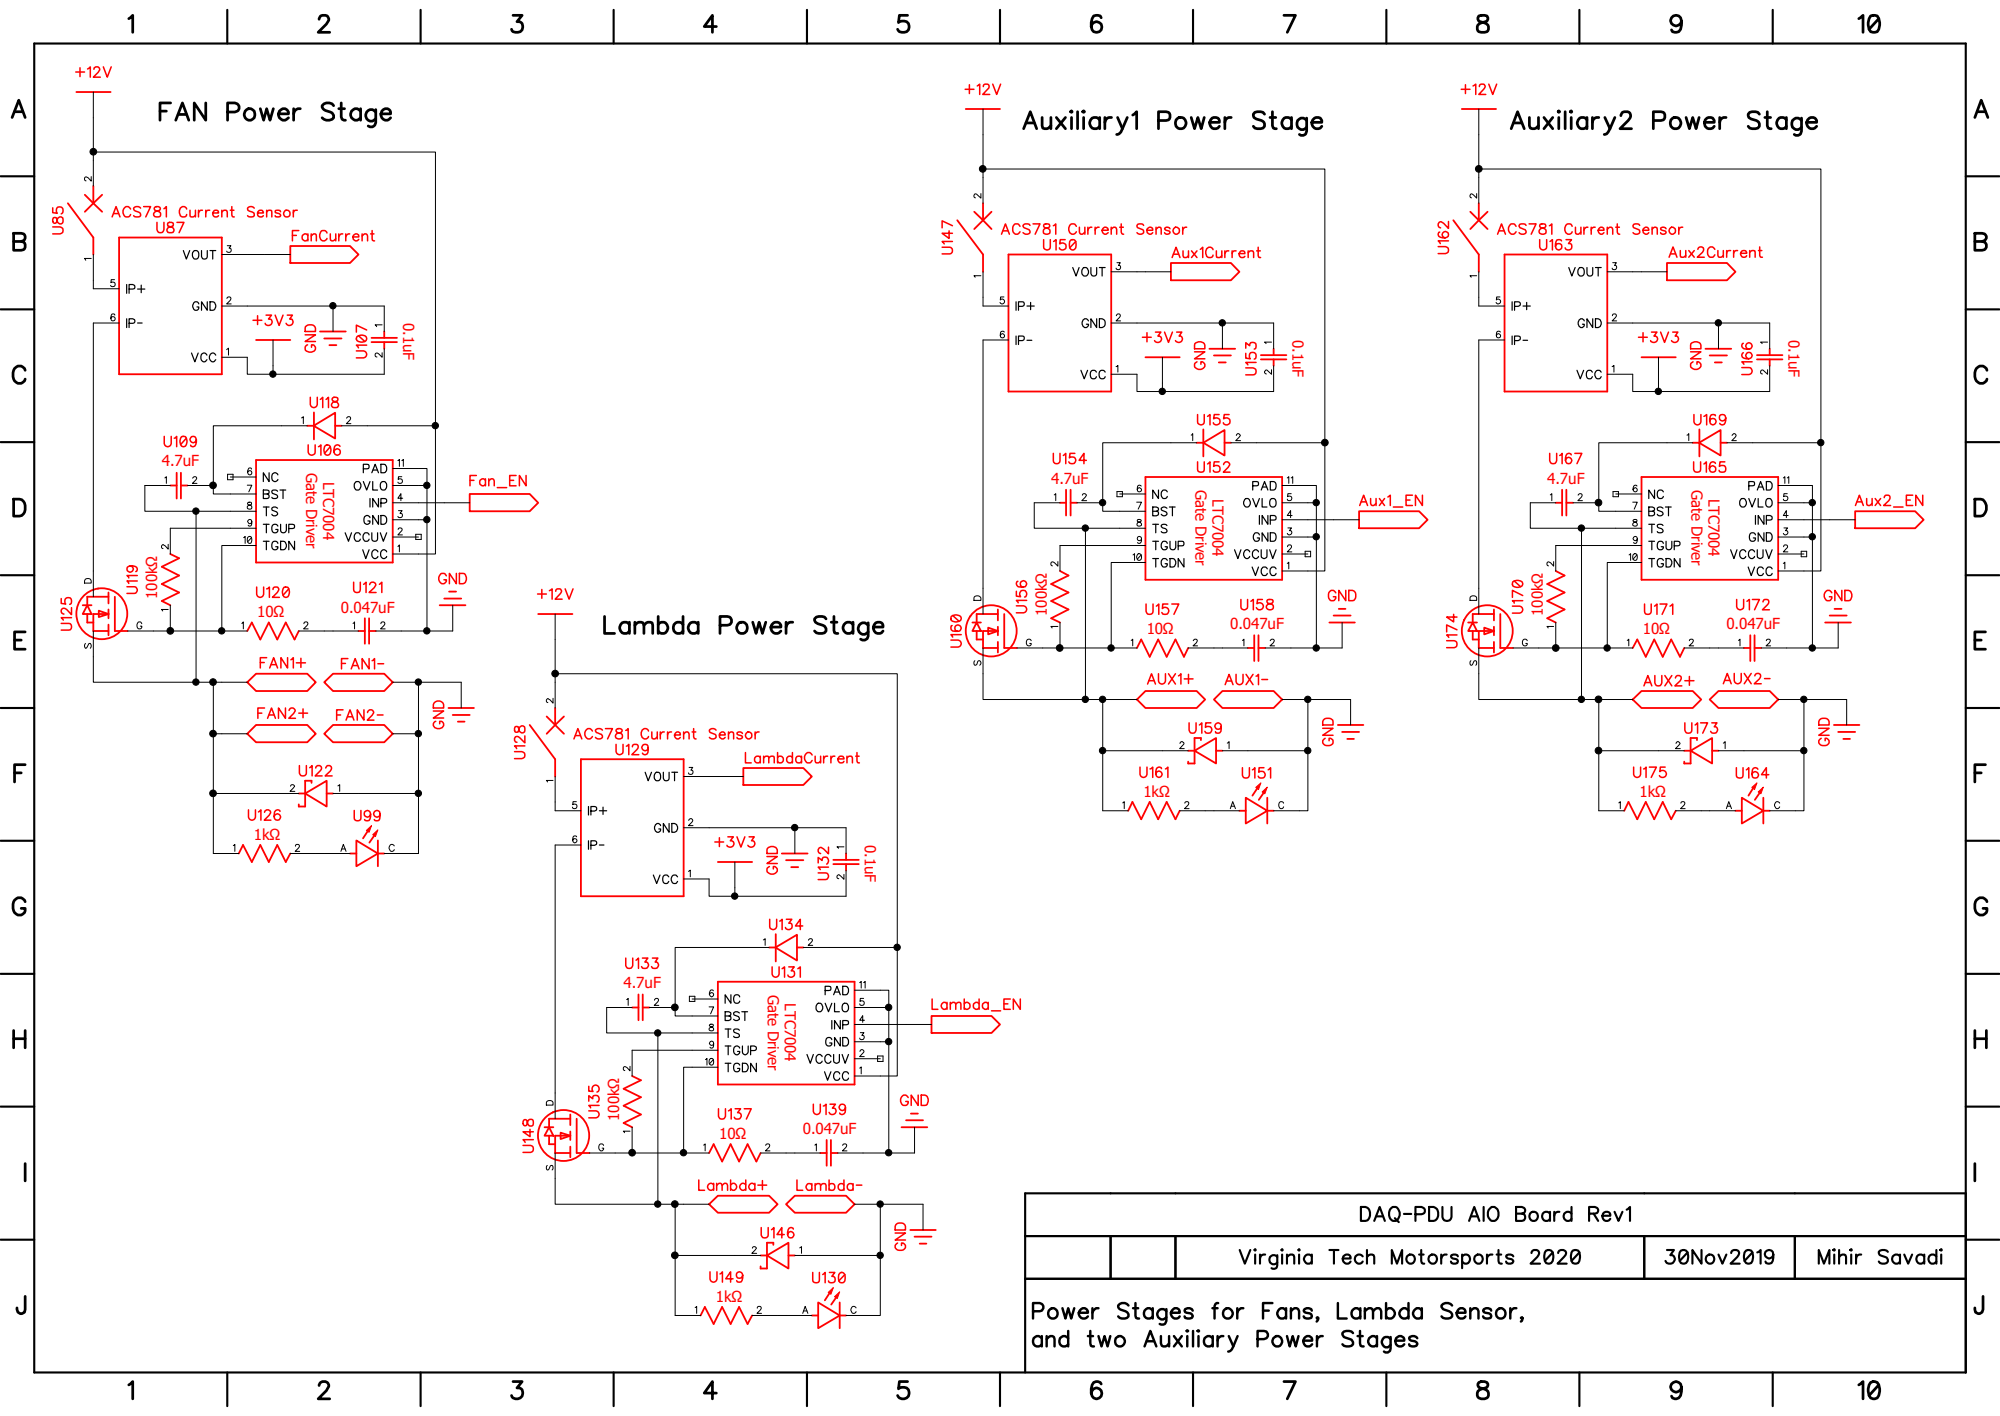
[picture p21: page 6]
LTC7004 Gate Driver 0.1uF; LTC7004 Gate Driver

Connector Terminals ¹kΩ 1kΩ 1kΩ ¹kΩ 1kΩ 1kΩ

TE Superseal Connector 60 pins (PCB Side) TE Superseal Connector 34 pins (PCB Side)

Battery, Starter, AC/DC

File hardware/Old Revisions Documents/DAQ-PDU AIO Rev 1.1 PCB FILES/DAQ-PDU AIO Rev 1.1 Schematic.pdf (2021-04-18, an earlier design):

SN65HVD230DR; CANBUS Transciever 0.1uF; 120 ohm ¹kΩ



# 4.7uF 100kΩ

1kΩ LTC7004 Gate Driver; LTC7004 Gate Driver

LTC7004; Gate Driver 100kΩ

LTC7004 Gate Driver 0.1uF; LTC7004 Gate Driver

Connector Terminals ¹kΩ 1kΩ 1kΩ ¹kΩ 1kΩ 1kΩ

TE Superseal Connector 60 pins (PCB Side) TE Superseal Connector 34 pins (PCB Side)

Battery, Starter, AC/DC

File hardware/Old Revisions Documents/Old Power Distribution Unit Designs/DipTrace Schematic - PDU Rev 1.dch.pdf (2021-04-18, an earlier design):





Main Solder Pad Array

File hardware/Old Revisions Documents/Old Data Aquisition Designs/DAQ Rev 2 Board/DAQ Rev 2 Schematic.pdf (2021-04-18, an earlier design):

CANBUS Adaptor & Solder Pads


# 4.7kΩ 1kΩ

4.7kΩ



Main Solder Pad Array connections) J1 (for inter-board TE SuperSeal Connector 60 Pins (for outside housing connections) J2 1kΩ 1kΩ 1kΩ 1kΩ 1kΩ 1kΩ

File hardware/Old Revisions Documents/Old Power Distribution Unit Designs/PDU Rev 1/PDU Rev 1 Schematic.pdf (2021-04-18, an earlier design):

1kΩ TC427 Gate Driver 1kΩ49.9Ω; TC427 Gate Driver 1kΩ

1kΩ49.9ΩTC427 Gate Driver 1kΩ; TC427 Gate Driver 1kΩ

1kΩ TC427 Gate Driver 1kΩ49.9Ω; 49.9Ω ¹kΩ; TC427 Gate Driver; 49.9Ω 1kΩ ¹kΩ


TE SuperSeal Connector 34 Pins (for outside housing connections⁾ J2; Battery & Starter Connector Terminals

Main Solder
Pad Array
(for inter-board
connections)

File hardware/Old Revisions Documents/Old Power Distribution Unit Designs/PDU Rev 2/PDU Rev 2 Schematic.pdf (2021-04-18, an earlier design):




StarterMotor PCB SolderPad Array

TE SuperSeal Connector 34 Pins (for outside housing connections)

DAQ PCB
Solder Pad Array


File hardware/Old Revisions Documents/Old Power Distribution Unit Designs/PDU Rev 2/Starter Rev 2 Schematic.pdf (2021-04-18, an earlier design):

1kΩ

1kΩ 1kΩ ¹kΩ; StarterMotor PCB SolderPad Array

Battery & Starter Connector Terminals

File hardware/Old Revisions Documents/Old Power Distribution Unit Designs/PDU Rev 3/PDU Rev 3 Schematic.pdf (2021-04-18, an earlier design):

# 4.7uF 100kΩ

LTC7004 Gate Driver; 1kΩ LTC7004 Gate Driver

LTC7004 Gate Driver 0.1uF; LTC7004 Gate Driver

LTC7004 Gate Driver 0.1uF; LTC7004 Gate Driver; 0.047uF LTC7004 Gate Driver

1kΩ 1kΩ ¹kΩ

Battery & Starter Connector Terminals LTC7004 Gate Driver



TE SuperSeal Connector 34 Pins (for outside housing connections) DAQ PCB

Solder Pad Array

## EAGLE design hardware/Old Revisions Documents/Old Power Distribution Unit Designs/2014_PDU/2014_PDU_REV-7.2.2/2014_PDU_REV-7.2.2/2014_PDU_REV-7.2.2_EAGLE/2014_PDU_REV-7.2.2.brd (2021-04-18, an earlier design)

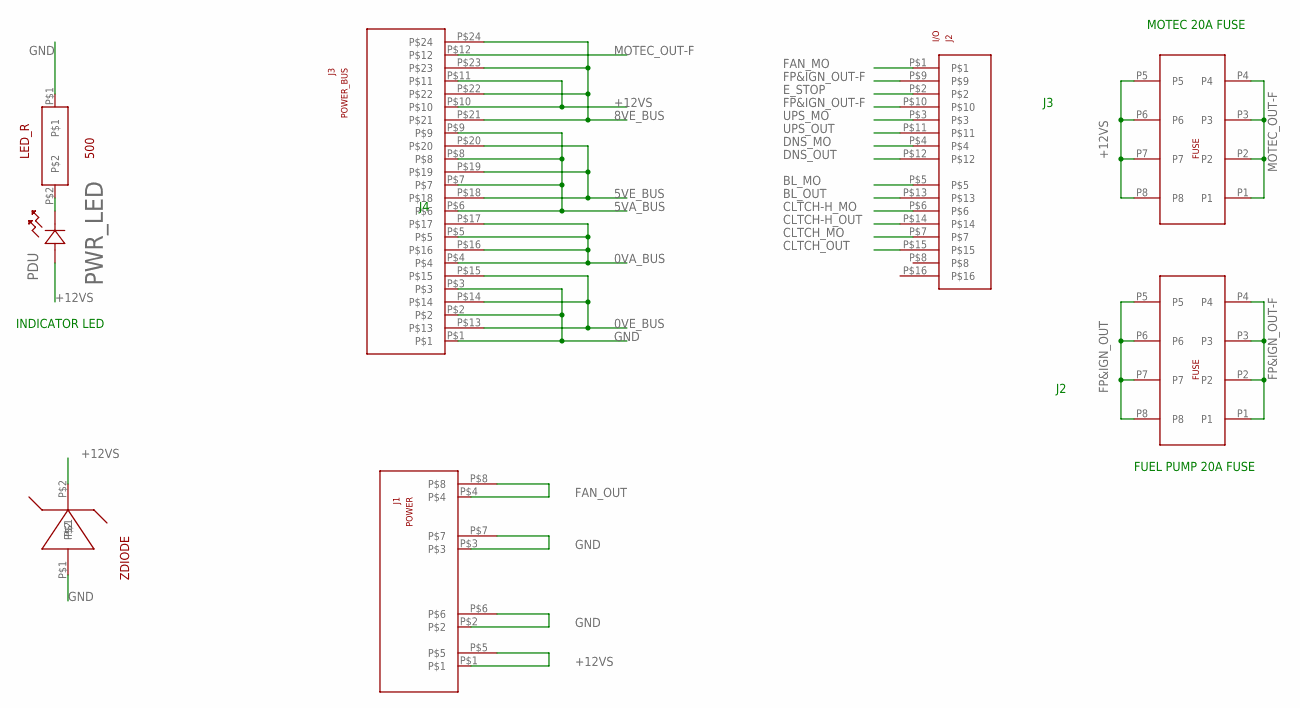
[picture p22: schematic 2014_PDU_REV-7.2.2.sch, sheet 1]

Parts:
I/O: J2; 39-30-1160
LED_R: 500; CRCW_2010_390R_JNEF
PDU: PWR_LED; LED_597-3111-407F
POWER: J1; 42820-4223
POWER_BUS: J3; 39-30-1240
U$1, U$2: 178.6165.0002
ZDIODE: DDZ20C-7

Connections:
0VA_BUS: POWER_BUS.P$4, POWER_BUS.P$5, POWER_BUS.P$16, POWER_BUS.P$17
0VE_BUS: POWER_BUS.P$13, POWER_BUS.P$14, POWER_BUS.P$15
5VA_BUS: POWER_BUS.P$6, POWER_BUS.P$7, POWER_BUS.P$8, POWER_BUS.P$9
5VE_BUS: POWER_BUS.P$18, POWER_BUS.P$19, POWER_BUS.P$20
8VE_BUS: POWER_BUS.P$21, POWER_BUS.P$22, POWER_BUS.P$23, POWER_BUS.P$24
+12VS: PDU.2, POWER.P$1, POWER.P$5, POWER_BUS.P$10, POWER_BUS.P$11, U$1.P5, U$1.P6, U$1.P7, U$1.P8, ZDIODE.P$2; also elsewhere on the board
BL_MO: I/O.P$5; also elsewhere on the board
BL_OUT: I/O.P$13; also elsewhere on the board
CLTCH-H_MO: I/O.P$6; also elsewhere on the board
CLTCH-H_OUT: I/O.P$14; also elsewhere on the board
CLTCH_MO: I/O.P$7; also elsewhere on the board
CLTCH_OUT: I/O.P$15; also elsewhere on the board
DNS_MO: I/O.P$4; also elsewhere on the board
DNS_OUT: I/O.P$12; also elsewhere on the board
E_STOP: I/O.P$2; also elsewhere on the board
FAN_MO: I/O.P$1; also elsewhere on the board
FAN_OUT: POWER.P$4, POWER.P$8; also elsewhere on the board
FP&IGN_OUT: U$2.P5, U$2.P6, U$2.P7, U$2.P8; also elsewhere on the board
FP&IGN_OUT-F: I/O.P$9, I/O.P$10, U$2.P1, U$2.P2, U$2.P3, U$2.P4
GND: LED_R.P$1, POWER.P$2, POWER.P$3, POWER.P$6, POWER.P$7, POWER_BUS.P$1, POWER_BUS.P$2, POWER_BUS.P$3, ZDIODE.P$1; also elsewhere on the board
MOTEC_OUT-F: POWER_BUS.P$12, U$1.P1, U$1.P2, U$1.P3, U$1.P4
unnamed: LED_R.P$2, PDU.1
UPS_MO: I/O.P$3; also elsewhere on the board
UPS_OUT: I/O.P$11; also elsewhere on the board

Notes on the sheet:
INDICATOR LED
MOTEC 20A FUSE
FUEL PUMP 20A FUSE

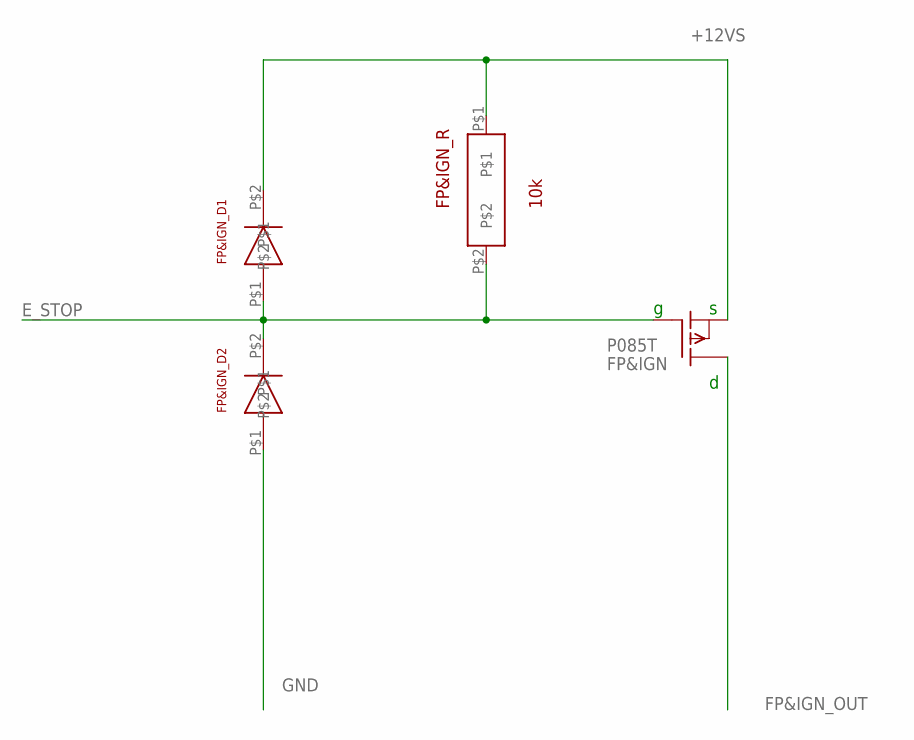
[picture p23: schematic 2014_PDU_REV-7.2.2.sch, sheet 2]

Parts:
FP&IGN: P085T; TO220
FP&IGN_D1, FP&IGN_D2: ER3JB-TP
FP&IGN_R: 10k; CRCW_2010_10K0_JNEF

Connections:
+12VS: FP&IGN.3 (S), FP&IGN_D1.P$2, FP&IGN_R.P$1; also elsewhere on the board
E_STOP: FP&IGN.1 (G), FP&IGN_D1.P$1, FP&IGN_D2.P$2, FP&IGN_R.P$2; also elsewhere on the board
FP&IGN_OUT: FP&IGN.2 (D); also elsewhere on the board
GND: FP&IGN_D2.P$1; also elsewhere on the board

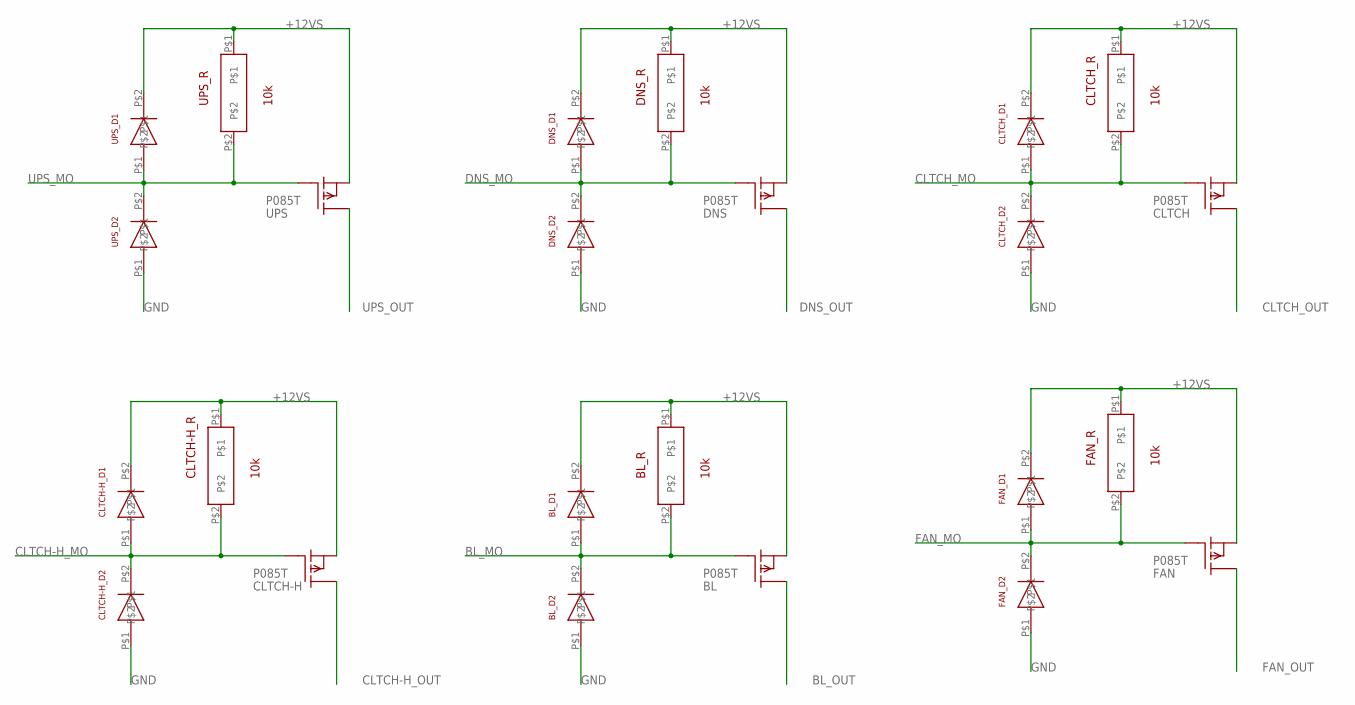
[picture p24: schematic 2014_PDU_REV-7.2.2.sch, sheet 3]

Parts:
BL: P085T; TO220
BL_D1, BL_D2: ER3JB-TP
BL_R: 10k; CRCW_2010_10K0_JNEF
CLTCH: P085T; TO220
CLTCH-H: P085T; TO220
CLTCH-H_D1, CLTCH-H_D2: ER3JB-TP
CLTCH-H_R: 10k; CRCW_2010_10K0_JNEF
CLTCH_D1, CLTCH_D2: ER3JB-TP
CLTCH_R: 10k; CRCW_2010_10K0_JNEF
DNS: P085T; TO220
DNS_D1, DNS_D2: ER3JB-TP
DNS_R: 10k; CRCW_2010_10K0_JNEF
FAN: P085T; TO220
FAN_D1, FAN_D2: ER3JB-TP
FAN_R: 10k; CRCW_2010_10K0_JNEF
UPS: P085T; TO220
UPS_D1, UPS_D2: ER3JB-TP
UPS_R: 10k; CRCW_2010_10K0_JNEF

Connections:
+12VS: BL.3 (S), BL_D1.P$2, BL_R.P$1, CLTCH.3 (S), CLTCH-H.3 (S), CLTCH-H_D1.P$2, CLTCH-H_R.P$1, CLTCH_D1.P$2, CLTCH_R.P$1, DNS.3 (S), DNS_D1.P$2, DNS_R.P$1, FAN.3 (S), FAN_D1.P$2, FAN_R.P$1, UPS.3 (S), UPS_D1.P$2, UPS_R.P$1; also elsewhere on the board
BL_MO: BL.1 (G), BL_D1.P$1, BL_D2.P$2, BL_R.P$2; also elsewhere on the board
BL_OUT: BL.2 (D); also elsewhere on the board
CLTCH-H_MO: CLTCH-H.1 (G), CLTCH-H_D1.P$1, CLTCH-H_D2.P$2, CLTCH-H_R.P$2; also elsewhere on the board
CLTCH-H_OUT: CLTCH-H.2 (D); also elsewhere on the board
CLTCH_MO: CLTCH.1 (G), CLTCH_D1.P$1, CLTCH_D2.P$2, CLTCH_R.P$2; also elsewhere on the board
CLTCH_OUT: CLTCH.2 (D); also elsewhere on the board
DNS_MO: DNS.1 (G), DNS_D1.P$1, DNS_D2.P$2, DNS_R.P$2; also elsewhere on the board
DNS_OUT: DNS.2 (D); also elsewhere on the board
FAN_MO: FAN.1 (G), FAN_D1.P$1, FAN_D2.P$2, FAN_R.P$2; also elsewhere on the board
FAN_OUT: FAN.2 (D); also elsewhere on the board
GND: BL_D2.P$1, CLTCH-H_D2.P$1, CLTCH_D2.P$1, DNS_D2.P$1, FAN_D2.P$1, UPS_D2.P$1; also elsewhere on the board
UPS_MO: UPS.1 (G), UPS_D1.P$1, UPS_D2.P$2, UPS_R.P$2; also elsewhere on the board
UPS_OUT: UPS.2 (D); also elsewhere on the board

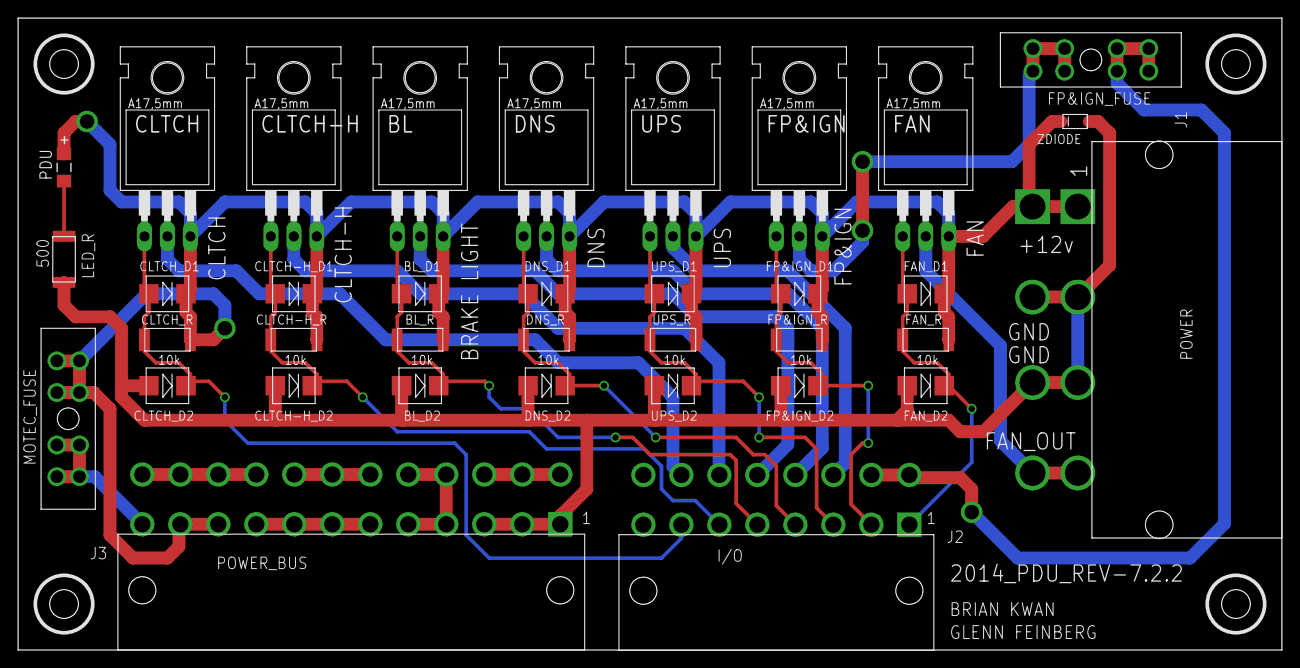
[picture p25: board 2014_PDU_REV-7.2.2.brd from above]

Board: 2 copper layers, 139.7 x 69.8 mm, 36 parts (0 on the bottom side), 24 nets.

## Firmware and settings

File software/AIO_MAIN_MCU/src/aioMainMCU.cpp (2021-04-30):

/* implementation for aioMainMCU class */

#include "aioMainMCU.hpp"

//floating point map helper function
float mapfl(float x, float in_min, float in_max, float out_min, float out_max) {
  return (x - in_min) * (out_max - out_min) / (in_max - in_min) + out_min;
}

// GPS Library Stuff. Must Setup outside class declaration strangely.
Adafruit_GPS GPS(&Serial3);
// IMU Library stuff. Must Setup outside class declaration strangely.
MPU9250 IMU(Wire1, 0x68);

aioMainMCU::aioMainMCU()
{
    //set up digital input pins
    pinMode(BSPDFAULT_IN, INPUT);
    pinMode(KILLSENSE_IN, INPUT);
    pinMode(DATALOG_BUTTON_IN, INPUT);
    pinMode(BUTTON_IN_NEUTRAL, INPUT);
    pinMode(BUTTON_IN_LAUNCHCONTROL, INPUT);
    pinMode(SD_CARD_DETECT, INPUT);

    //set up ADC input ports for analog input at 12bits
    analog_init();
    analogReadResolution(12);
    analogReadAveraging(5); //set no. of averaging per read.

    //setup GPS
    GPS.begin(9600);
    GPS.sendCommand(PMTK_SET_NMEA_OUTPUT_RMCGGA); //ask for type of data
    GPS.sendCommand(PMTK_SET_NMEA_UPDATE_10HZ); //set 10Hz update rate
    GPS.sendCommand(PGCMD_ANTENNA); //request update on antenna

    //setup IMU
    this->sigIns.IMUbeginStatus = IMU.begin();
    if (this->sigIns.IMUbeginStatus < 0)
    {
        this->errorPresent = true;
        this->errorstring.concat("IMU init unsuccessful statVal: " + 
                                  String(this->sigIns.IMUbeginStatus) + ERDELIM);
    }
    // setting the accelerometer full scale range to +/-8G 
    IMU.setAccelRange(MPU9250::ACCEL_RANGE_8G);
    // setting the gyroscope full scale range to +/-500 deg/s
    IMU.setGyroRange(MPU9250::GYRO_RANGE_500DPS);
    // setting DLPF bandwidth to 20 Hz
    IMU.setDlpfBandwidth(MPU9250::DLPF_BANDWIDTH_20HZ);
    // setting SRD to 19 for a 50 Hz update rate
    IMU.setSrd(19);

    //setup SD card 
    // (add first line on startup to give guide to whats in each column)
    // see logAllInputs() method for order of entry
    pinMode(SPI_CS_0, OUTPUT);
    if (!SD.begin(SPI_CS_0))
    {
        this->errorPresent = true;
        this->errorstring.concat("SD card not present and cant be initialized"
            + ERDELIM);
    }
    this->dataFile = SD.open("datalog.csv", FILE_WRITE);
    if (!this->dataFile)
    {
        this->errorPresent = true;
        this->errorstring.concat("Error opening datalog file" + ERDELIM);
    }
    else
    {
        String firstLine;

        firstLine.concat("shiftSolenoid Current (Amps), ");
        firstLine.concat("GSensor Current (Amps), ");
        firstLine.concat("syncSensor Current (Amps), ");
        firstLine.concat("EGT Current (Amps), ");
        firstLine.concat("injector Current (Amps), ");
        firstLine.concat("turboSolenoid Current (Amps), ");
        firstLine.concat("LTC Current (Amps), ");
        firstLine.concat("fuelPump Current (Amps), ");
        firstLine.concat("ignitionCoil Current (Amps), ");
        firstLine.concat("fan Current (Amps), ");
        firstLine.concat("auxiliaryStage Current (Amps), ");
        firstLine.concat("motec Current (Amps), ");
        firstLine.concat("acdcConverter Current (Amps), ");
        firstLine.concat("battery Current (Amps), ");
        firstLine.concat("servo Current (Amps), ");

        firstLine.concat("acdcConverter Voltage (Volts), ");
        firstLine.concat("battery Voltage (Volts), ");

        firstLine.concat("gearSense ADC read, ");
        firstLine.concat("throttleSignal ADC read, ");
        firstLine.concat("brakeSignal ADC read, ");
        firstLine.concat("bspdFault Digital read, ");
        firstLine.concat("killsense Digital read, ");
        firstLine.concat("dataLogButtonPressed Digital read, ");
        firstLine.concat("neutralButtonPressed Digital read, ");
        firstLine.concat("launchButtonPressed Digital read, ");
        firstLine.concat("sdCardDetected Digital read, ");

        firstLine.concat("year GPSdata (GMT), ");
        firstLine.concat("month GPSdata (GMT), ");
        firstLine.concat("day GPSdata (GMT), ");
        firstLine.concat("hour GPSdata (GMT), ");
        firstLine.concat("min GPSdata (GMT), ");
        firstLine.concat("sec GPSdata (GMT), ");
        firstLine.concat("mSec GPSdata (GMT), ");
        firstLine.concat("gpsFix GPSdata (T/F), ");
        firstLine.concat("fixQual GPSdata (0:Invalid; 1:GPS; 2:DGPS), ");
        firstLine.concat("fixQual3d GPSdata (1:Nofix; 2:2D fix; 3:3D fix), ");
        firstLine.concat("sats GPSdata (no. of satellites in use), ");
        firstLine.concat("latDeg GPSdata (decimal degrees), ");
        firstLine.concat("longDeg GPSdata (decimal degrees), ");
        firstLine.concat("altitude GPSdata (meters above MSL), ");
        firstLine.concat("speed GPSdata (knots), ");
        firstLine.concat("angle GPSdata (course degrees from true north), ");
        firstLine.concat("magVar GPSdata (magnetic variation in degrees vs true north), ");
        firstLine.concat("hdop GPSdata (horizontal relative accuracy), ");
        firstLine.concat("vdop GPSdata (horizontal relative accuracy), ");
        firstLine.concat("pdop GPSdata (horizontal relative accuracy), ");

        firstLine.concat("accelX IMUdata (m/(s^2)), ");
        firstLine.concat("accelY IMUdata (m/(s^2)), ");
        firstLine.concat("accelZ IMUdata (m/(s^2)), ");
        firstLine.concat("gyroX IMUdata (rad/s), ");
        firstLine.concat("gyroY IMUdata (rad/s), ");
        firstLine.concat("gyroZ IMUdata (rad/s), ");
        firstLine.concat("magX IMUdata (uT), ");
        firstLine.concat("magY IMUdata (uT), ");
        firstLine.concat("magZ IMUdata (uT), ");
        firstLine.concat("IMU_dieTemp IMUdata (C), ");

        if(this->errorPresent)
        {
            firstLine.concat(String("NO ERRORS PRESENT"));
        }
        else
        {
            firstLine.concat("ERRORS PRESENT: " + this->errorstring);
        }

        this->dataFile.println(firstLine);
    }
}

void aioMainMCU::readInputs()
{
    //read all current data
    this->current.shiftSolenoid  = ampsFromADC(analogRead(CURRENT_SHIFTSOL));
    this->current.GSensor        = ampsFromADC(analogRead(CURRENT_GSENSOR));
    this->current.syncSensor     = ampsFromADC(analogRead(CURRENT_SYNC));
    this->current.EGT            = ampsFromADC(analogRead(CURRENT_EGT));
    this->current.injector       = ampsFromADC(analogRead(CURRENT_INJECTOR));
    this->current.turboSolenoid  = ampsFromADC(analogRead(CURRENT_TURBOSOL));
    this->current.LTC            = ampsFromADC(analogRead(CURRENT_LTC));
    this->current.fuelPump       = ampsFromADC(analogRead(CURRENT_FP));
    this->current.ignitionCoil   = ampsFromADC(analogRead(CURRENT_IC));
    this->current.fan            = ampsFromADC(analogRead(CURRENT_FAN));
    this->current.auxiliaryStage = ampsFromADC(analogRead(CURRENT_AUX));
    this->current.motec          = ampsFromADC(analogRead(CURRENT_MOTEC));
    this->current.acdcConverter  = ampsFromADC(analogRead(CURRENT_ACDC));
    this->current.battery        = ampsFromADC(analogRead(CURRENT_BATTERY));
    this->current.servo          = ampsFromADC(analogRead(CURRENT_SERVO));

    //read all voltage data
    this->voltage.acdcConverter = mapfl(analogRead(VOLTAGE_ACDC), 0, 4096, 0, 3.3)*5
                                    + V_OFFSET;
    this->voltage.battery       = mapfl(analogRead(VOLTAGE_BATTERY), 0, 4096, 0, 3.3)*5
                                    + V_OFFSET;

    //read all signalInput data
    this->sigIns.gearSense            = analogRead(GEARSENSE_ADC_IN);
    this->sigIns.throttleSignal       = analogRead(THROTTLE_SIG_IN);
    this->sigIns.brakeSignal          = analogRead(BRAKE_SIG_IN);
    this->sigIns.bspdFault            = digitalReadFast(BSPDFAULT_IN);
    this->sigIns.killsense            = digitalReadFast(KILLSENSE_IN);
    this->sigIns.dataLogButtonPressed = digitalReadFast(DATALOG_BUTTON_IN);
    this->sigIns.neutralButtonPressed = digitalReadFast(BUTTON_IN_NEUTRAL);
    this->sigIns.launchButtonPressed  = digitalReadFast(BUTTON_IN_LAUNCHCONTROL);
    this->sigIns.sdCardDetected       = digitalReadFast(SD_CARD_DETECT);

    //read all GPS data
    GPS.read();
    this->sigIns.year       = GPS.year;
    this->sigIns.month      = GPS.month;
    this->sigIns.day        = GPS.day;
    this->sigIns.hour       = GPS.hour;
    this->sigIns.min        = GPS.minute;
    this->sigIns.sec        = GPS.seconds;
    this->sigIns.mSec       = GPS.milliseconds;
    this->sigIns.gpsFix     = GPS.fix;
    this->sigIns.fixQual    = GPS.fixquality;
    this->sigIns.fixQual3d  = GPS.fixquality_3d;
    this->sigIns.sats       = GPS.satellites;
    this->sigIns.latDeg     = GPS.latitudeDegrees;
    this->sigIns.longDeg    = GPS.longitudeDegrees;
    this->sigIns.altitude   = GPS.altitude;
    this->sigIns.speed      = GPS.speed;
    this->sigIns.angle      = GPS.angle;
    this->sigIns.magVar     = GPS.magvariation;
    this->sigIns.hdop       = GPS.HDOP;
    this->sigIns.vdop       = GPS.VDOP;
    this->sigIns.pdop       = GPS.PDOP;

    //read all IMU data
    IMU.readSensor();
    this->sigIns.accelX = IMU.getAccelX_mss();
    this->sigIns.accelY = IMU.getAccelY_mss();
    this->sigIns.accelZ = IMU.getAccelZ_mss();
    this->sigIns.gyroX  = IMU.getGyroX_rads();
    this->sigIns.gyroY  = IMU.getGyroY_rads();
    this->sigIns.gyroZ  = IMU.getGyroZ_rads();
    this->sigIns.magX   = IMU.getMagX_uT();
    this->sigIns.magY   = IMU.getMagY_uT();
    this->sigIns.magZ   = IMU.getMagZ_uT();
    this->sigIns.IMU_dieTemp = IMU.getTemperature_C();
}

void aioMainMCU::logAllInputs()
{
    String dataLine;

    if(this->dataFile)
    {
        // current data
        dataLine.concat(String(this->current.shiftSolenoid) + ", ");
        dataLine.concat(String(this->current.GSensor) + ", ");
        dataLine.concat(String(this->current.syncSensor) + ", ");
        dataLine.concat(String(this->current.EGT) + ", ");
        dataLine.concat(String(this->current.injector) + ", ");
        dataLine.concat(String(this->current.turboSolenoid) + ", ");
        dataLine.concat(String(this->current.LTC) + ", ");
        dataLine.concat(String(this->current.fuelPump) + ", ");
        dataLine.concat(String(this->current.ignitionCoil) + ", ");
        dataLine.concat(String(this->current.fan) + ", ");
        dataLine.concat(String(this->current.auxiliaryStage) + ", ");
        dataLine.concat(String(this->current.motec) + ", ");
        dataLine.concat(String(this->current.acdcConverter) + ", ");
        dataLine.concat(String(this->current.battery) + ", ");
        dataLine.concat(String(this->current.servo) + ", ");

        // voltage data
        dataLine.concat(String(this->voltage.acdcConverter) + ", ");
        dataLine.concat(String(this->voltage.battery) + ", ");

        // signal input data
        dataLine.concat(String(this->sigIns.gearSense) + ", ");
        dataLine.concat(String(this->sigIns.throttleSignal) + ", ");
        dataLine.concat(String(this->sigIns.brakeSignal) + ", ");
        dataLine.concat(String(this->sigIns.bspdFault) + ", ");
        dataLine.concat(String(this->sigIns.killsense) + ", ");
        dataLine.concat(String(this->sigIns.dataLogButtonPressed) + ", ");
        dataLine.concat(String(this->sigIns.neutralButtonPressed) + ", ");
        dataLine.concat(String(this->sigIns.launchButtonPressed) + ", ");
        dataLine.concat(String(this->sigIns.sdCardDetected));

        // GPS data
        dataLine.concat(String(this->sigIns.year) + ", ");
        dataLine.concat(String(this->sigIns.month) + ", ");
        dataLine.concat(String(this->sigIns.day) + ", ");
        dataLine.concat(String(this->sigIns.hour) + ", ");
        dataLine.concat(String(this->sigIns.min) + ", ");
        dataLine.concat(String(this->sigIns.sec) + ", ");
        dataLine.concat(String(this->sigIns.mSec) + ", ");
        dataLine.concat(String(this->sigIns.gpsFix) + ", ");
        dataLine.concat(String(this->sigIns.fixQual) + ", ");
        dataLine.concat(String(this->sigIns.fixQual3d) + ", ");
        dataLine.concat(String(this->sigIns.sats) + ", ");
        dataLine.concat(String(this->sigIns.latDeg) + ", ");
        dataLine.concat(String(this->sigIns.longDeg) + ", ");
        dataLine.concat(String(this->sigIns.altitude) + ", ");
        dataLine.concat(String(this->sigIns.speed) + ", ");
        dataLine.concat(String(this->sigIns.angle) + ", ");
        dataLine.concat(String(this->sigIns.magVar) + ", ");
        dataLine.concat(String(this->sigIns.hdop) + ", ");
        dataLine.concat(String(this->sigIns.vdop) + ", ");
        dataLine.concat(String(this->sigIns.pdop) + ", ");

        // IMU data
        dataLine.concat(String(this->sigIns.accelX) + ", ");
        dataLine.concat(String(this->sigIns.accelY) + ", ");
        dataLine.concat(String(this->sigIns.accelZ) + ", ");
        dataLine.concat(String(this->sigIns.gyroX) + ", ");
        dataLine.concat(String(this->sigIns.gyroY) + ", ");
        dataLine.concat(String(this->sigIns.gyroZ) + ", ");
        dataLine.concat(String(this->sigIns.magX) + ", ");
        dataLine.concat(String(this->sigIns.magY) + ", ");
        dataLine.concat(String(this->sigIns.magZ) + ", ");
        dataLine.concat(String(this->sigIns.IMU_dieTemp) + ", ");

        if(this->errorPresent)
        {
            dataLine.concat(String("NO ERRORS PRESENT"));
        }
        else
        {
            dataLine.concat("ERRORS PRESENT: " + this->errorstring);
        }
    }
    else
    {
        this->errorPresent = true;
        this->errorstring.concat("error opening datalog.csv" + ERDELIM);
        
        dataLine.concat("ERRORS PRESENT: " + this->errorstring);
    }

    this->dataFile.println(dataLine);
    this->dataFile.flush();
}

bool const aioMainMCU::getError(String &errorDescription)
{
    errorDescription = this->errorstring;
    return this->errorPresent;
}

float const aioMainMCU::ampsFromADC(uint16_t ADC_reading)
{
    //see file:///C:/Users/m_sav/Downloads/ACS781-Datasheet.pdf page 2
    // we are running ACS781KLRTR-150B-T which has a 8.8mV/A sensitivity.
    // So we do a floating point scale of ADC_reading, which as input range of
    // 0 to 4096, to an output range of 0 to 3300mV (since the ADC scales linearly from
    // 0 to 3.3V max), then dividing by the ACS781 current sensor data sheet constant
    // of 8.8mV/A, then add to C_OFFSET for calibration.
    return (mapfl(ADC_reading, 0, 4096, 0, 3300) / 8.8) - C_OFFSET;;
}

void const aioMainMCU::printToMonitor() 
{
    Serial.print("BattV: " + String(mapfl(analogRead(VOLTAGE_BATTERY), 0, 4096, 0, 3.3)*5) + "V");
    // Serial.println(", BattA: " + String(this->ampsFromADC(analogRead(CURRENT_BATTERY))) + "A");
    Serial.println(", BattA: " + String(analogRead(CURRENT_BATTERY)) + "A");
}

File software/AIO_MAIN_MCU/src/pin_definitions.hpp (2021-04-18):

#ifndef PIN_DEFINITIONS_CPP
#define PIN_DEFINITIONS_CPP

/* 
    Mihir Savadi 18 April 2021
    File containing all pin definitions for DAQ_PDU AIO BOARD REV 2
*/

// UART PORTS
#define RX1_DASH 0
#define TX1_DASH 1

#define RX3_GPS 7
#define TX3_GPS 8

#define RX9_TELEMETRY 9
#define TX9_TELEMETRY 10

#define RX4_DRS_MCU 31
#define TX4_DRS_MCU 32

// SPI PORTS
#define SPI_MOSI_0 11
#define SPI_MISO_0 12
#define SPI_SCK_0  13
#define SPI_CS_0   15

// I2C PORTS
#define SCL1 37
#define SDA1 38

// CANBUS PORTS
#define CANBUS_TX       29
#define CANBUS_RX       30
#define CANSPEEDSELECT  24

// DIGITAL SIGNAL INPUTS
#define BSPDFAULT_IN            2
#define KILLSENSE_IN            4
#define DATALOG_BUTTON_IN       5
#define BUTTON_IN_NEUTRAL       25
#define BUTTON_IN_LAUNCHCONTROL 26
#define SD_CARD_DETECT          27

// ANALOG SIGNAL INPUTS
#define STEERPOS_IN      3 //this is not an ADC port. Hardware error. Do not use.

#define GEARSENSE_ADC_IN A10

#define THROTTLE_SIG_IN  A2
#define BRAKE_SIG_IN     A3

#define VOLTAGE_ACDC     A16
#define VOLTAGE_BATTERY  A17

#define CURRENT_SHIFTSOL A0
#define CURRENT_GSENSOR  A11
#define CURRENT_SYNC     A21
#define CURRENT_EGT      A22
#define CURRENT_INJECTOR A25
#define CURRENT_TURBOSOL A26
#define CURRENT_LTC      A20
#define CURRENT_FP       A4
#define CURRENT_IC       A5
#define CURRENT_FAN      A6
#define CURRENT_AUX      A7
#define CURRENT_MOTEC    A8
#define CURRENT_ACDC     A9
#define CURRENT_BATTERY  A14
#define CURRENT_SERVO    A15


#endif

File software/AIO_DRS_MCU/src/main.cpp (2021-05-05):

/* Mihir Savadi 18th April 2021 */

#include <Arduino.h>

#include "aioDRSMCU.hpp"

void setup() {

  //following macro block control in "aioDRSMCU.hpp" header 
  #if includeSerialPrints == true
    Serial.begin(9600);
  #endif

  aioDRSMCU drsMCU;

  // drsMCU.manualServoControl(false);
  
  while(1)
  {
    drsMCU.runDRSservo(true);
    drsMCU.runBBservo();
  }
}

//dont use this. Put all looped code in the while(1) block in void setup for
// tighter control of scope and to just keep code clean.
void loop() {}

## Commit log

2021-04-18 added more todos and gps imu functionality skeletons
2021-04-18 added NKK M2028TJW01-GA-1A - the brake bias toggle switch that the DRS MCU is built around - to the BOM
    [DAQ-PDU AIO Rev 2 BOM.xlsx]
2021-04-26 added first iteration of setup sd card column header print
2021-04-27 added an extra method and macro to make conversion of ADC values from current sensor to amps easy for logging. also added code to convert adc from voltage reads to volt units
2021-04-27 fixed silly rundrs errors
    [aioDRSMCU.cpp]
2021-04-27 turned on serial prints
2021-04-27 removed commas to fix csv stuff
    [aioMainMCU.cpp]
2021-04-27 added point on servo fuse
2021-04-30 added a serial print helper function. also tested for current sensor offset constant by running starter motor in bay. Just subtracted average DC offset in idle from sensor reading. simple dimple.
2021-05-01 cleaned up some code, trivial bracket edits
2021-05-03 changed sensor in bom from 150U to 050B
    [DAQ-PDU AIO Rev 2 BOM.xlsx]
2021-05-05 added method and functionality in aioDRSMCU class of manual control of servos through serial monitor for testing and wing mount setup
2021-05-05 set servo positions

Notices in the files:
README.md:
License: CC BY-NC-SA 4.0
